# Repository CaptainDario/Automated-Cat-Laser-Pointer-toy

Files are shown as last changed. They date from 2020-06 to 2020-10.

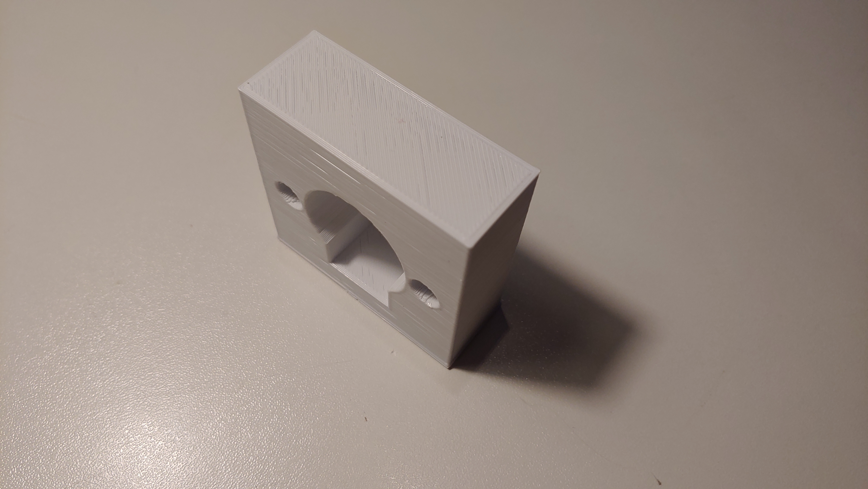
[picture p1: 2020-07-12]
instructions/images/20200623_044347_HDR.jpg

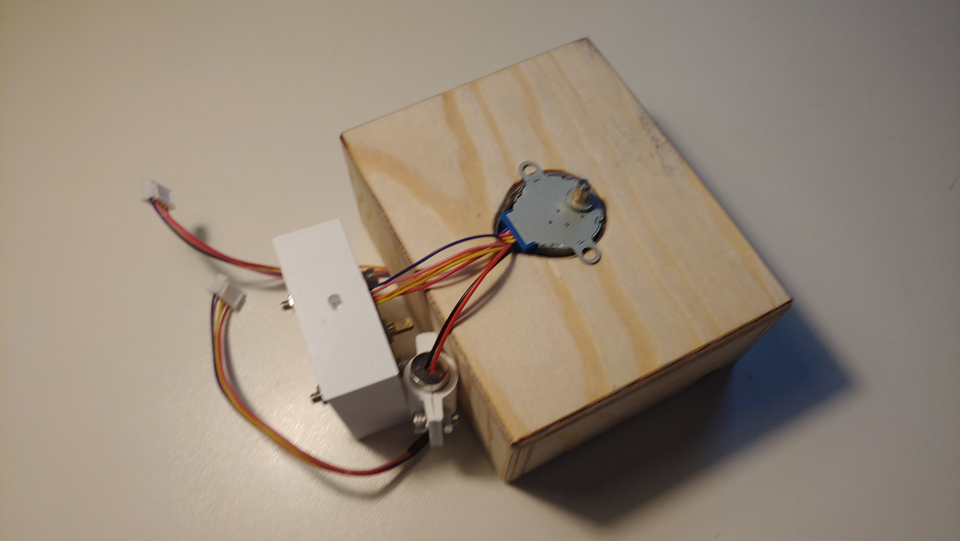
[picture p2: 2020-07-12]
instructions/images/20200623_051316_HDR.jpg

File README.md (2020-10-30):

"DaPetToy" is an automated pet-Laser-Pointer toy.
It randomly moves a laser pointer on two axes so that a pet could chase it.

I made this for the 2020 ["Pets Speed Challenge"]((https://www.instructables.com/id/An-Automated-Cat-laser-pointer-toy/) ) on instructables (The instructable has more images for the setup of the hardware).
See it in action by clicking on the image below. </br>
See it in action (https://www.youtube.com/watch?v=vp5igMt3IM0)

## Instructions

## Flashing the software
You can compile the software from source and flash the data and firmware this way.
But here I will describe how to flash the software via the ready-made images provided [here.](https://github.com/CaptainDario/Automated-Cat-Laser-Pointer-toy/releases) </br>
First you will need a [python install](https://www.python.org) with the [esptool](https://github.com/espressif/esptool) module installed.
```
path\to\your\python.exe -m pip install esptool
```
Now you are ready to write the firmware and data image:
```
path\to\your\python.exe -m esptool -b 921600 write_flash 0x0 firmware.bin 0x00300000 spiffs.bin
```

**Caution:** </br>
Depending on the esp board you are using the offset where to write the 'spiffs.bin' can be different!

Now you can power up your esp.
After some time it should open a access point called 'DaPetToy'.
The webserver IP address is the standard esp webserver address: </br>
```192.168.4.1``` </br>
Enter it in your browser and you will be greeted with a screen to enter you WiFi credentials.
The ESP will reboot after submission of the credentials.
If everything is correct you can now look up the ip address of your ESP and connect to it from your home network.

But for now you have to do the following:You need to rename the file “REMOVE_credentials.h” in the “src” folder to “credentials.h”. And replace “YOUR SSID” and “YOUR PWD” in this file with your wifi SSID and password.
After completing this first step you have to upload the file system to the esp and than compile and upload the software.

## Hardware
You need following hardware for this project:

* [3.3V laser pointer](https://www.aliexpress.com/item/32676284654.html?spm=a2g0s.9042311.0.0.27424c4dB5clXD)
* [ESP D1 mini](https://www.aliexpress.com/item/33036965281.html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,searchweb201602_,searchweb201603_)
* Some jumper wires
* [barrel jack for power](https://www.aliexpress.com/item/32883658107.html?spm=a2g0s.9042311.0.0.27424c4dngOKlg)
* 2x [ULN2003 stepper motors with driver board](https://www.aliexpress.com/item/32962476866.html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,searchweb201602_,searchweb201603_)
* [5V 2A PSU](https://www.aliexpress.com/item/4000102102421.html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,searchweb201602_,searchweb201603_)
* 1x M4×10 screw and nut
* 2x M4×20 screw, nut and washer
* 3D printer
(All those components are just examples)

First you need to print the mounts for the motors. 
When you downloaded the newest release it will contain a folder called 'models' which will contain the necessary .stl files.

A little bit harder will be the making of the base case. I made the case out of wood to provide more structural rigidity (and I think it looks nicer too). The base case has one large hole on the top and a small one on the side. The large hole is for the stepper motor and the small one for the power input. Make sure that the motor-hole is large enough to fit the cables of two stepper motors and also the two wires of the laser pointer (they need space to move freely as the wires will move due to the rotation).

Now connect the components as shown in this image:

![circuit.png](./instructions/wiring/circuit.png)

Now it is time to assemble it. First put the laser pointer in the mount and use the M4x10 screw and nut to fix it in place.
Next up is the power jack. Put it in the small hole and fasten it with its nut.
The first motor has to be put in the 3D printed mount and secured with the two M4×20 screws, nuts and washers.
In the second last step the other motor has to be placed in the large hole of the wood case while routing all the cables through the hole too.
Finally put the motors in their holes and also stick them together. If they do not fit tightly put some hot glue on them to secure everything in place.

#### Caution
* Double check that the cables have enough space to move while the motors are rotating. 
* NEVER rotate the motors by hand! You can and most probably will damage them.
* Motors tend to overheat during extend usage. Since this is a cat toy, stop it if it is not in use to prevent it from overheating.

## Project Ideas and next steps
You can take a look at the planned tasks [here](https://github.com/CaptainDario/Automated-Cat-Laser-Pointer-toy/projects/1).
If you have ideas for new features or improvements feel free to open a request.

## Developer notes
This project uses [Circuit Daiagram](https://www.circuit-diagram.org/) for wiring images.

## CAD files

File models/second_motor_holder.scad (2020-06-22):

include <metrics.scad>


module second_motor_holder(){

    difference(){
        //the main mount of the motor
        cube([motor_d + motor_mount_w + motor_hole_w * 2,
            motor_h + mount_wall_thickness,
            motor_d + motor_mount_w + laser_pointer_holder_l]);

        translate([0, -mount_wall_thickness, (motor_d + motor_mount_w + laser_pointer_holder_l) / 2]){
            motor_hole();
        }
        
        //hole for the knob of the motor on the base plate
        translate([(motor_d + motor_mount_w + motor_hole_w * 2) / 2 - motor_ending_h/2,
                (laser_pointer_holder_l) / 2 - motor_ending_w/2,
                -preview_margin]){
            cube([motor_ending_h, motor_ending_w, motor_ending_l]);
        }
    }
}

module motor_hole(){
    //motor (round section)
    translate([(motor_d + motor_mount_w + motor_hole_w*2) / 2,
            0,
            0]){
        rotate([90, 0, 180]){
            cylinder(h=motor_h, d1=motor_d, d2=motor_d);
        }
    }
    //motor (square section)
    translate([(motor_d + motor_mount_w + motor_hole_w*2) / 2 - motor_square_w/2,
           0,
            //middle of circle - diameter of circle / 2 - halfe of the square part / 2
            - motor_d / 2 - motor_square_h/2]){
            cube([motor_square_w, motor_h, motor_square_h]);
    }

    //holes for screws
    space_next_to_hole = (motor_d + motor_mount_w + motor_hole_w * 2 - motor_d) / 2;
    //left
    translate([-motor_hole_w/2 + space_next_to_hole,
            0,
            0]){
        rotate([90, 0, 180]){
            cylinder(h=laser_pointer_holder_l + motor_hole_w + preview_margin*2,
                    d1=motor_mount_w, d2=motor_mount_w,
                    $fn=_fn);
        }
    }
    //right
    translate([motor_hole_w/2 + space_next_to_hole + motor_d,
            0,
            0]){
        rotate([90, 0, 180]){
            cylinder(h=laser_pointer_holder_l + motor_hole_w + preview_margin*2,
                    d1=motor_mount_w, d2=motor_mount_w,
                    $fn=_fn);
        }
    }

}

//test
second_motor_holder();


//animation
$vpt = [(motor_d + motor_mount_w + motor_hole_w * 2) / 2,
            laser_pointer_holder_l / 2,
            (motor_d + motor_mount_w + laser_pointer_holder_l) / 2];

$vpr = [60, 0, 360 * $t];

$vpd = 400;

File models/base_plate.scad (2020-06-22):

include <metrics.scad>

use <second_motor_holder.scad>

component_cut_out_depth = 1.5;
wall_thickness = 6.5;

driver_board_w = 33;
driver_board_l = 35;

gap_between_components = 5;

base_plate_w = driver_board_w * 2 + gap_between_components * 4 + motor_d;
base_plate_base_h = component_cut_out_depth + 1;
base_plate_h = component_cut_out_depth + motor_h;


//d1 mini dimensions
esp_w = 36;
esp_l = 26;

usb_c_jack_w = 9;
usb_c_jack_h = 4.5;

//the amount of magnets per side
amount_of_magnets = 3;
magnet_d = 5.5;
magnet_h = 2.5;



difference(){
    //base case(body)
    cube([base_plate_w + 2*wall_thickness, base_plate_w + 2*wall_thickness, component_cut_out_depth + 1 + motor_h]);
    //remove inside
    translate([wall_thickness, wall_thickness, component_cut_out_depth + 1]) {
        cube([base_plate_w, base_plate_w, base_plate_h]);
    }

    translate([0, 0, base_plate_base_h - component_cut_out_depth + preview_margin]){
        //space for USB jack
        translate([base_plate_w/2, -preview_margin, component_cut_out_depth]){
            cube([usb_c_jack_w, wall_thickness + 2*preview_margin, usb_c_jack_h]);
        }
        //holes for the motor-drivers
        //left
        translate([wall_thickness,
                    base_plate_w/2 + wall_thickness - driver_board_l/2,
                    0]){
            cube([driver_board_w, driver_board_l, component_cut_out_depth]);
        }
        //right
        translate([wall_thickness + base_plate_w -driver_board_w,
                    base_plate_w/2 + wall_thickness - driver_board_l/2,
                    0]){
            cube([driver_board_w, driver_board_l, component_cut_out_depth]);
        } 
        //hole for the esp
        translate([wall_thickness + base_plate_w/2 - esp_w/2,
                    wall_thickness + base_plate_w - esp_l,
                    0]){
            cube([esp_w, esp_l, component_cut_out_depth]);
        }
        //motor hole
        translate([wall_thickness + base_plate_w/2 - motor_d,
                wall_thickness + base_plate_w/2,
                0]) {
            rotate([90, 0, 0]){
                motor_hole();
            }
        }
    }

    //top magnets
    translate([0, 0, component_cut_out_depth + 1 + motor_h - magnet_h + preview_margin]) {
        magnets();
    }

    //bottom magnets
    translate([0, 0, -preview_margin]) {
        magnets();
    }
}


module magnets(){
    //magnet holes
    magnet_spacing = ((base_plate_w + 2*wall_thickness - magnet_d) / amount_of_magnets) - (wall_thickness/2 - magnet_d/2)/(amount_of_magnets-1);
    for (x = [0:amount_of_magnets]) {
        for (y = [0:amount_of_magnets]){
            if (y == 0 || y == amount_of_magnets || x == 0 || x ==amount_of_magnets) {
                translate([(wall_thickness/2 - magnet_d/2 + magnet_d/2) + x * magnet_spacing,
                        (wall_thickness/2 - magnet_d/2 + magnet_d/2) + y * magnet_spacing,
                        0]){
                    cylinder(h=magnet_h, d1=magnet_d, d2=magnet_d);
                }
            }
        }
    }
}

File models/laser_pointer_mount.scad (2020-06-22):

include <metrics.scad>



module laser_pointer_holder(){
    union(){

        //motor mount
        difference(){
            //holder
            translate([-(motor_mount_thickness + laser_pointer_d/2),
                        -laser_pointer_d/4,
                        0]){
                cube([motor_mount_thickness, laser_pointer_d/2, laser_pointer_holder_l]);
            }

            //hole
            translate([- laser_pointer_d/2 - motor_mount_thickness - preview_margin,
                        -motor_ending_w/2,
                        laser_pointer_holder_l/2 + motor_ending_h/2]) {

                rotate([0, 90, 0]){
                    cube([motor_ending_h, motor_ending_w, motor_ending_l]);
                }
            }
        }

        //laser pointer hole
        difference(){
            //shell
            cylinder(h=laser_pointer_holder_l,
                    d1=laser_pointer_d + mount_wall_thickness*2, d2=laser_pointer_d + mount_wall_thickness*2, $fn=_fn);

            //remove space for the pointer
            translate([0, 0, -preview_margin]) {
                cylinder(h=laser_pointer_holder_l + preview_margin*2, d1=laser_pointer_d, d2=laser_pointer_d, $fn=_fn);
            };

            //space for the screw to fasten
            translate([0, -mount_wall_thickness/2, -preview_margin]){
                cube([laser_pointer_d/2 + mount_wall_thickness, mount_wall_thickness, laser_pointer_holder_l + 2*preview_margin]);
            }
        }

        //fastener
        difference(){
            union(){
                //left side of the screw terminal
                translate([laser_pointer_d/2, -mount_wall_thickness * 3/2 - preview_margin, 0]){
                    cube([screw_terminal_length, mount_wall_thickness, laser_pointer_holder_l]);
                }

                //right side of the screw terminal
                translate([laser_pointer_d/2, mount_wall_thickness/2 + preview_margin, 0]){
                    cube([screw_terminal_length, mount_wall_thickness, laser_pointer_holder_l]);
                }
            }

            //cut out a screw
            translate([laser_pointer_d/2 + screw_terminal_length/2, laser_pointer_d/2, laser_pointer_holder_l/2]) {
                rotate([90, 0, 0]){
                    cylinder(h=laser_pointer_d, d1=screw_d, d2=screw_d, $fn=_fn);
                }
            }
        }
    }
}

//main
laser_pointer_holder();
//animation
$vpt = [0, 0, laser_pointer_holder_l/2];

$vpr = [60, 0, 360 * $t];

$vpd = 200;

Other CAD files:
models/metrics.scad

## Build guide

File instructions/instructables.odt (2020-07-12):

I guess all cat owners know the struggle: the moment you sit down and want to enjoy your favorite TV-show, the cat thinks “I need someone to play with me”.
Would it not be awesome if you could just pull auto your smartphone and start an automagically rotating laser pointer?
I thought so and therefore build one. It consist of two motors which can move the laser pointer on two axis. One can set via a web-server the degrees which the motor is allowed to rotate.
If I caught your attention read further and build your own!

Supplies:

- laser pointer
- Uln2003 driver and motor
- Esp8266 D1 mini
- Barrel jack for power input
- Jump-Wire cables
- 5V 2A PSU
- Some wood
- 1x M4×10 screw and nut
- 2x M4×20 screw, nut and washer

Tools:

- 3D printer
- basic wood working tools

Files:

- motor mounts

Firmware repo

# 1 Building and assembling the necessary parts

First we need to print the mounts for the motors. To do this print the files which were mentioned in the introduction.
A little bit harder will be the making of the base case. I made the case out of wood to provide more structural rigidity (and I think it looks nicer too). The base case has one large hole on the top and a small one on the side. The large hole is for the stepper motor and the small one for the power input. Make sure that the motor-hole is large enough to fit the cables of two stepper motors and also the two wires of the laser pointer (they need space to move freely as the wires will move due to the rotation).

Now it is time to assemble it. First put the laser pointer in the mount and use the M4x10 screw and nut to fix it in place.
Next up is the power jack. Put it in the small hole and fasten it with its nut.
The first motor has to be put in the 3D printed mount and secured with the two M4×20 screws, nuts and washers.

In the second last step the other motor has to be placed in the large hole of the wood case while routing all the cables through the hole too.

Finally put the motors in their holes and also stick them together. If they do not fit tightly put some hot glue on them to secure everything in place.

Hint:

Double check that the cables have enough space to move while the motors are rotating.

# 2 Connecting the electronics

The motor which rotates the laser pointer needs to be connected to the pins D5, D6, D7 and D0 of the esp. The pins of the other motor need to be connected to the pins D1, D2, D3 and D4. Also do not forget to connect the 5V and GND of both motors, the ESP and the laser pointer to the barrel jack.

# 3 Flashing the Firmware

To flash the firmware download it from my github repository. You need to rename the file “REMOVE_credentials.h” in the “src” folder to “credentials.h”. And replace “YOUR SSID” and “YOUR PWD” in this file with your wifi SSID and password.
After completing this first step you have to upload the file system to the esp and than compile and upload the software.

Because the procedure of flashing does differ from software to software you are on your own regarding this point. But here are guides for Visual Studio Code using PlatformIO:

- upload filesystem (https://docs.platformio.org/en/latest/platforms/espressif8266.html#uploading-files-to-file-system-spiffs)
- flash firmware (https://docs.platformio.org/en/latest/integration/ide/vscode.html#quick-start)

# 4 Using the Device

Finally we have reached the point where we can use the device!
When the esp is powered up and you visit its IP-address you will see an interface like the image shown here. There is basically just one mode. This moves the motors randomly around. However you can limit their movement.
Firstly, one starts the movement by pressing the “ON”-button and stops it with the “OFF” button. This button also stops other movements.
The “LEFT”-button moves the matching motor “left” and the “RIGHT”-button “right”.
You can limit the movement for every motor like the following:

1. press “LEFT” for the motor you want to limit
2. wait until the motor reaches the position you want to set and press “OFF”
3. press the “MINIMUM” button of the motor, this sets the current position as the origin
4. now press “RIGHT” of the same motor and wait until it reaches the second position
5. press “MAXIMUM” this saves the current position as the end point
6. press on and the motor will only move in the set bounds

The origin and the endpoint are the maximum values the motor can move to and thus limiting the rotation.

Some notes:

- When power is removed from the esp the calibration has to be redone
- watch out that the cables always have enough space to move around

# 5 Watch uninterrupted your TV show

Was it worth all the effort just to watch TV without your cat?
Maybe not.
Can this device help bring some joy to your cat?

I hope so.

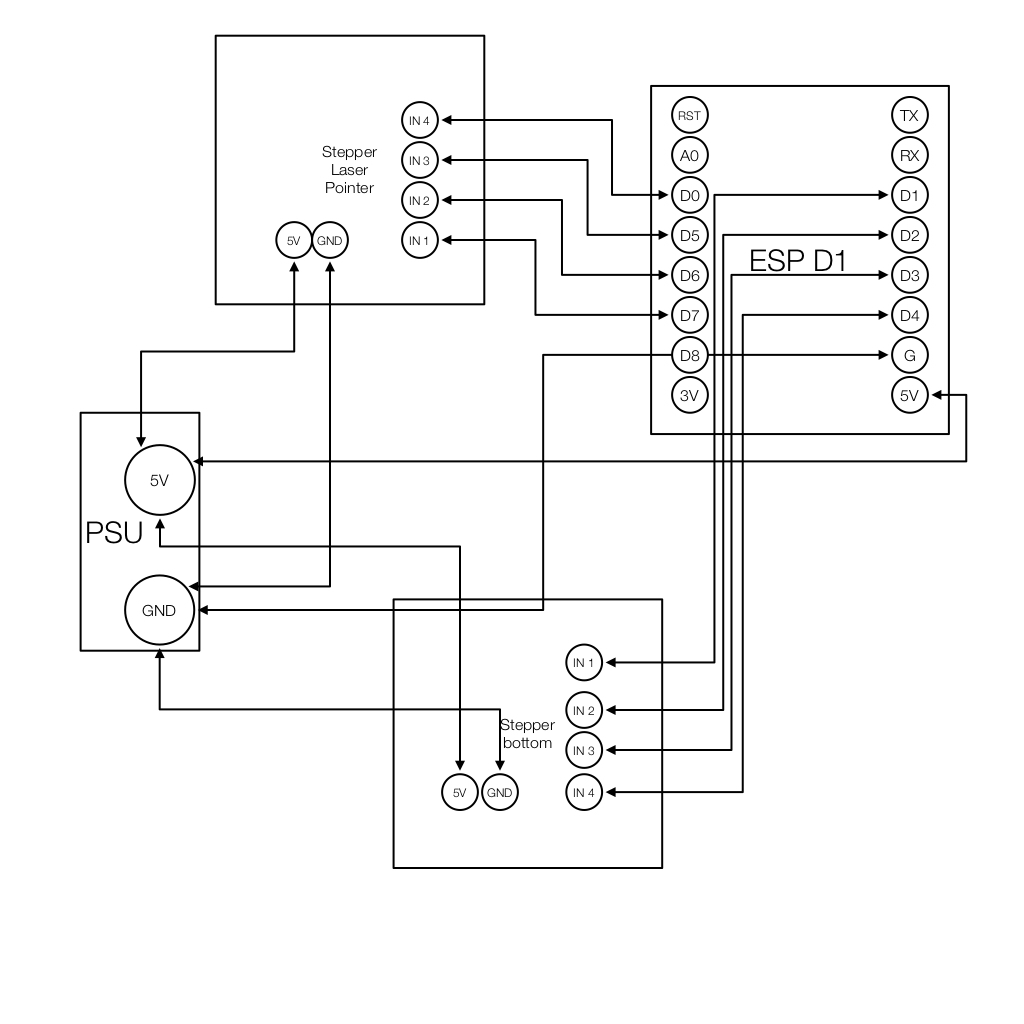
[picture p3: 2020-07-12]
instructions/images/wiring.png

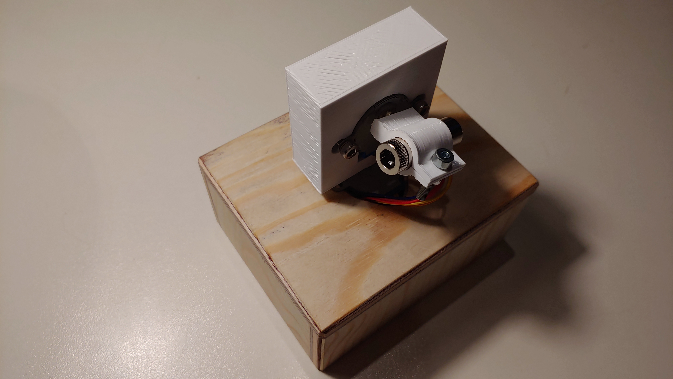
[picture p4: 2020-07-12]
instructions/images/20200623_034800_HDR.jpg

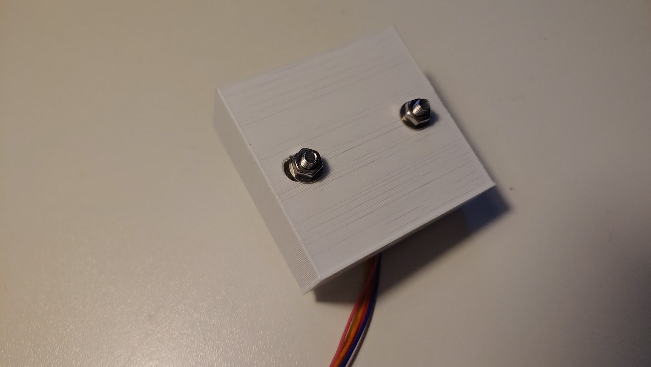
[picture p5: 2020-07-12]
instructions/images/20200623_051015_HDR.jpg

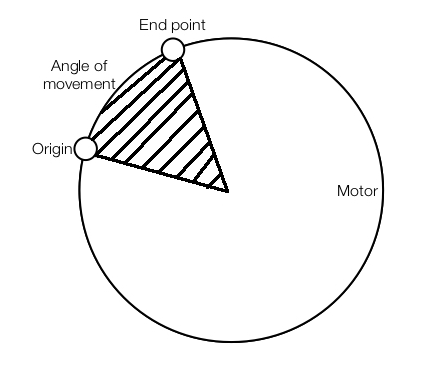
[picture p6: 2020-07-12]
instructions/images/origin_end_point_idea.png

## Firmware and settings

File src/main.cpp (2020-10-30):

#include <Arduino.h>

//custom
#include <stepper.h>
#include <webserver.h>


/**
 set the limits the user entered in the UI
*/
void set_limits();
/**
 Configure the motors to run ind
*/
void configuration();
/**
 Initialize stepper 1 (bottom)
*/
void setup_motor_bottom();
/**
 Initialize stepper 2 (top/laser pointer)
*/
void setup_motor_top();




void setup() {
  Serial.begin(460800);
  WiFi.setAutoConnect(true);

  //disable laser at boot
  pinMode(D8, OUTPUT);
  //randomize values
  pinMode(A0, INPUT);
  randomSeed(analogRead(A0));

  // Initialize SPIFFS
  if(!SPIFFS.begin()){
    Serial.println("An Error has occurred while mounting SPIFFS");
    return;
  }

  try_connect_to_wifi();
  get_nearby_networks(); 
  setup_webserver();

  //initialize stepper motors 
  setup_motor_bottom();
  setup_motor_top();

  Serial.println("Setup finished");
}

void loop() {
  //check if motors need to be enabled
  enable_motor_for_movement();

  //rotate the motors randomly
  if(rotating){
    if (stepper_bottom.distanceToGo() == 0)
    {
        delay(min_delay_before_new_pos_bottom);
        // set a random position
        int rnd;
        if(stepper_bottom_max > 0)
          rnd = random(0, stepper_bottom_max);
        else
          rnd = random(stepper_bottom_max, 0);

        Serial.print("bottom: "); Serial.println(rnd);
        stepper_bottom.moveTo(rnd);
    }
    stepper_bottom.run();

    if (stepper_top.distanceToGo() == 0)
    {
        delay(min_delay_before_new_pos_top);
        // set a random position
        int rnd;
        if(stepper_top_max > 0)
          rnd = random(0, stepper_top_max);
        else
          rnd = random(stepper_top_max, 0);

        Serial.print("top: "); Serial.println(rnd);
        stepper_top.moveTo(rnd);
    }
    stepper_top.run();
  }  

  set_limits();
  configuration();
  
  try_connect_to_wifi();
    
}

void setup_motor_bottom(){
  stepper_bottom.setMaxSpeed(2000);
  stepper_bottom.setAcceleration(2000);
  stepper_bottom.setSpeed(2000);
}

void setup_motor_top(){
  stepper_top.setMaxSpeed(2000);
  stepper_top.setAcceleration(2000);
  stepper_top.setSpeed(2000);
}

void configuration(){
  //bottom
  if(move_bottom_left){
    stepper_bottom.moveTo(stepper_bottom.currentPosition() + 5);
    stepper_bottom.run();
  }
  if(move_bottom_right){
    stepper_bottom.moveTo(stepper_bottom.currentPosition() - 5);
    stepper_bottom.run();
  }
  //top
  if(move_top_right){
    stepper_top.moveTo(stepper_top.currentPosition() + 5);
    stepper_top.run();
  }
  if(move_top_left){
    stepper_top.moveTo(stepper_top.currentPosition() - 5);
    stepper_top.run();
  }
}

void set_limits(){
  if (set_bottom_minimum)
  {
    stepper_bottom.setCurrentPosition(0);
    set_bottom_minimum = false;
    Serial.print(stepper_top.currentPosition());
  }
  if (set_bottom_maximum)
  {
    stepper_bottom_max = stepper_bottom.currentPosition();
    set_bottom_maximum = false;
    Serial.print(stepper_bottom_max);
  }
  if (set_top_minimum)
  {
    stepper_top.setCurrentPosition(0);
    set_top_minimum = false;
    Serial.print(stepper_top.currentPosition());
  }
  if (set_top_maximum)
  {
    stepper_top_max = stepper_top.currentPosition();
    set_top_maximum = false;
    Serial.print(stepper_top_max);
  }
}

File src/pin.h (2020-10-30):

#include <Arduino.h>

int LASER_PIN = 017; //D8

int stepper_bottom_pin_1 = D1; 
int stepper_bottom_pin_2 = D3; 
int stepper_bottom_pin_3 = D2; 
int stepper_bottom_pin_4 = D4; 

int stepper_top_pin_1 = D5; 
int stepper_top_pin_2 = D7; 
int stepper_top_pin_3 = D6; 
int stepper_top_pin_4 = D0; 

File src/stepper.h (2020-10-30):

#include <AccelStepper.h>
#include <pin.h>

//motor bottom
AccelStepper stepper_bottom = AccelStepper(8, stepper_bottom_pin_1, stepper_bottom_pin_2,
                                              stepper_bottom_pin_3, stepper_bottom_pin_4);
int stepper_bottom_max = 1000;
int min_delay_before_new_pos_bottom = 50;

//motor top
AccelStepper stepper_top = AccelStepper(8, stepper_top_pin_1, stepper_top_pin_2, 
                                            stepper_top_pin_3, stepper_top_pin_4);
int stepper_top_max = 1000;
int min_delay_before_new_pos_top = 50;


//current state (true -> rotating | false -> not rotating)
bool rotating = false;
bool move_bottom_right = false;
bool move_bottom_left = false;
bool move_top_right = false;
bool move_top_left = false;

//set the limits
bool set_bottom_minimum = false;
bool set_bottom_maximum = false;
bool set_top_minimum = false;
bool set_top_maximum = false;

String current_state = String();


/*
Set the string on the webserver which indicates indicates the current state.
*/
String set_state(const String& var);
/*
Disbles all movement instructions to the motors.
This should help prevent them from overheating.
*/
void disable_all_movement();
/*
Enables the motors only when a movement is requried.
This should help prevent them from overheating.
*/
void enable_motor_for_movement();



String set_state(const String& var){

  current_state = String();

  if(var == "STATE"){
    if(rotating){
      current_state = "Running";
    }
    else if(move_bottom_left || move_bottom_right ||
          set_bottom_minimum || set_bottom_maximum){
      current_state = "callibrating bottom";
    }
    else if(move_top_left || move_top_right ||
          set_top_minimum || set_top_maximum){
      current_state = "callibrating top";
    }
    else{
      current_state = "Idle";
    }
  }
  return current_state;
}

void disable_all_movement(){

  rotating = false;
  move_bottom_right = false;
  move_bottom_left  = false;
  move_top_right    = false;
  move_top_left     = false;

  stepper_top.disableOutputs();
  stepper_bottom.disableOutputs();
}

void enable_motor_for_movement(){

  if(move_bottom_right || move_bottom_left)
    stepper_bottom.enableOutputs();

  if(move_top_right || move_top_left)
    stepper_top.enableOutputs();

  if(rotating){
    stepper_top.enableOutputs();
    stepper_bottom.enableOutputs();
  }
}

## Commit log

2020-06-22 Do not track the credentials entered
2020-06-23 corrected stepper motor
2020-06-24 removed print
2020-06-24 ignore .stl
    [base_plate.stl, laser_pointer_mount.stl, second_motor_holder.stl]
2020-06-24 renamed stepper variables for better readability
    also moved initialization to its own function
2020-06-25 Corrected random values for "negative" rotations
    [main.cpp]
2020-06-25 Initialize random with the value of the unconnected A0 pin
2020-06-25 moved steppers to stepper.h
2020-06-25 added function to prevent overheating
    [stepper.h]
2020-06-25 added disable and enable of the motors to prevent overheating
2020-07-12 added spacer for table
2020-07-12 disable the laser when the toy boots
2020-07-12 added global pin variables
2020-07-12 use the pin variables instead of fixed pins
    [stepper.h]
2020-07-12 added possibility to toggle laser on and off
2020-07-12 changed to arduino definitions
2020-07-12 added wiring files
2020-07-22 added wiring images
2020-07-29 updated for better visuals of tables and buttons
2020-07-29 switching to a web server to enter credentials
2020-07-31 automatically toggle the laser with the motors
2020-08-05 included css for the landing zone
2020-08-05 removed special case for IE because of deprecation
2020-10-30 current software version
2020-10-30 current values
2020-10-30 do not print wifi password on command line
2020-10-30 updated info for the stl files
